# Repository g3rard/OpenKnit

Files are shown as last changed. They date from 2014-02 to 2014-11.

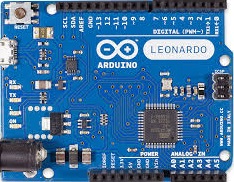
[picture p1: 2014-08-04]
Wally120/3Dmodel/OBJ_format/Wally120/Auduino_Leonardo_01.jpg

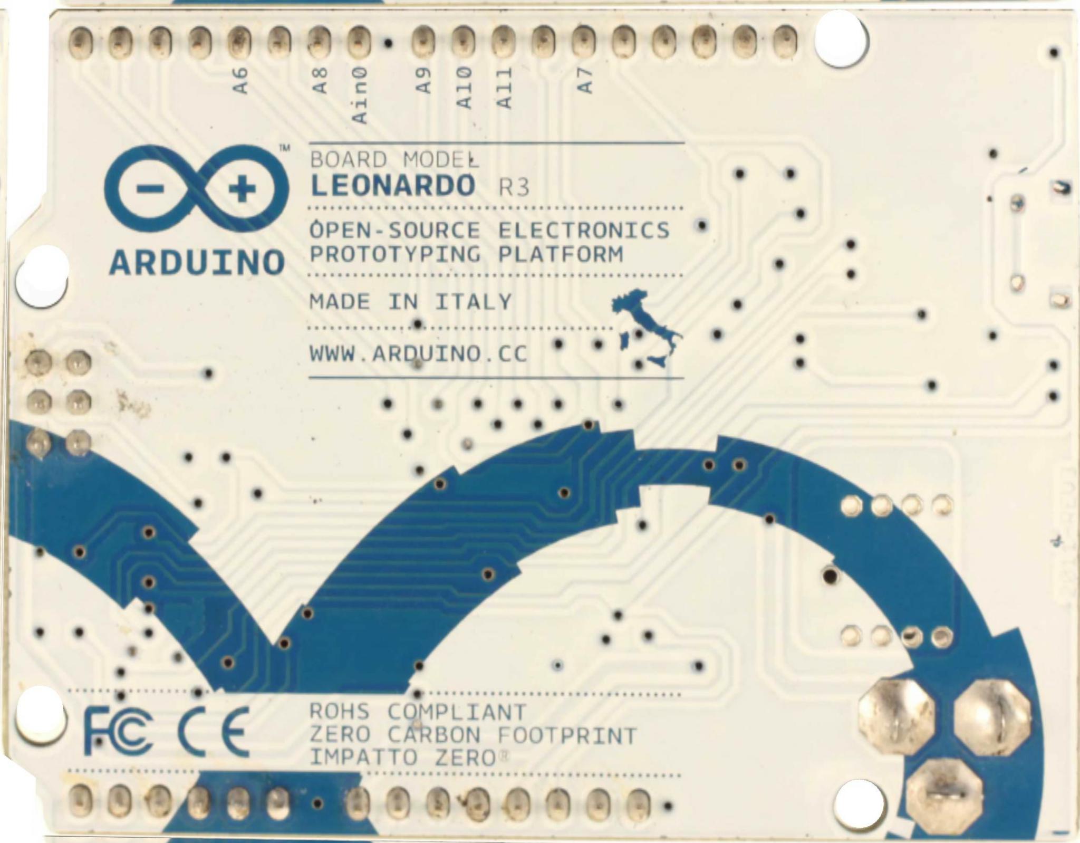
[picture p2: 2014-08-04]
Wally120/3Dmodel/OBJ_format/Wally120/Arduino_rear_1.jpg

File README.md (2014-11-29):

OpenKnit is a project that offers a new digital fabrication tool, an open-source knitting machine that can create ready-to-wear clothes from digital files. 

The documentation for the Wally340 is outdated, currently working on the development of the Wally120 since itÕs cheaper, smaller, easier to assemble and it works better. Although, the improvements of the Wally120 can be scaled up if you want to create bigger garments.

WARNING: this project is at an early stage of development, every piece of hardware and software is in beta version, testing and testing, if you are an adventurer this is a place for you.

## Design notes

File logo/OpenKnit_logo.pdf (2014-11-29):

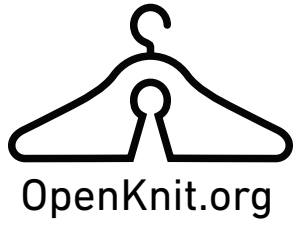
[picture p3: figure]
OpenKnit.org

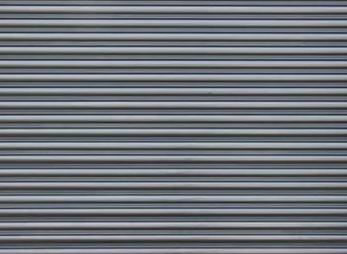
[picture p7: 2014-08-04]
Wally120/3Dmodel/OBJ_format/Wally120/M3.jpg

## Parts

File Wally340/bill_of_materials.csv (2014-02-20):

COMPONENT | UNITS | PRICE (€) | PROVIDER
 |  |  | LOCAL (Barcelona)
methacrylate | 1015x1525x3mm | 60 | http://plasticexpress.es/
lasercut | 1 | 100 | http://fablabbcn.org/
aluminum T profile 15x15 | 3582mm | 10.78 | http://www.hiperaluminio.com/
aluminum I profile 20x3 | 5505mm | 13.76 | http://www.hiperaluminio.com/
plastic parts | 500gr | 12.07 | http://www.reprapbcn.com/catalog/index.php/material-pla/pla-3mm.html
Arduino Leonardo | 1 | 21.78 | http://www.diotronic.com/raspberry-pi-arduino/arduino/placas/arduino-leonardo-w-headers_r_1080_26762.aspx
microinterrupter | 2 | 2.84 | http://www.diotronic.com/componentes-mecanicos/interruptores-conmutadores-pulsadores/microrruptores-final-de-carrera/microrrup-miniatura-3a125v-c-p_r_194_1820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
photo relfective sensor | 1 | 1.29 | http://www.ondaradio.es/producto/cny70-rohs-refleoptcouplgaas-ir-infrared-emitt-diodeplastcase-23579.aspx
hall effect sensor | 2 | 2.56 | http://www.ondaradio.es/producto/a1106euat-rohs-transistor-efecto-hall-sip-3-27327.aspx
bearing 608 | 1 | 2 | local hardware store or skateshop
threaded rod | 881mm | 1.5 | local hardware store
nuts and bolts | many | 20 | local hardware store
 |  |  | SPAIN
aluminum X profile 20x20 | 6870mm | 26.68 | http://www.motedis.es/shop/Perfil-ranurado/Perfil-20-Tipo-B-ranura-6/Perfil-20x20-Tipo-B-ran-6::999991.html
aluminum X profile 30x30 | 3000mm | 20.29 | http://www.motedis.es/shop/Perfil-ranurado/Perfil-30-Tipo-B-ranura-8/Perfil-30x30-Tipo-B-ran-8::99999432.html
aluminum X profile 40x40 | 3582mm | 34.76 | http://www.motedis.es/shop/Perfil-ranurado/Perfil-40-Tipo-I-ranura-8/Perfil-40x40L-Tipo-I-ran-8::999999.html
 |  |  | EUROPE (UK)
needles | 380 | 104.5 | http://www.bsk.co.uk/knitmastersilver-reed-sk120--sr120-xkn8-763-p.asp
 |  |  | CHINA (Aliexpress)
stepper driver A4988 | 1 | 5.28 | http://www.aliexpress.com/item/Stepstick-A4988-for-3D-printer-with-heat-sink-Reprap-Stepper-motor-driver-order-4-pcs-price/1053639333.html
stepper motor nema17 | 1 | 10.91 | http://www.aliexpress.com/item/4-Leads-Nema-17-Stepper-Motor-2800g-cm-12VDC-0-4A-CNC-Cutting-and-Mill-of/536727302.html
servomotor SG90 | 5 | 7.85 | http://www.aliexpress.com/item/Hot-sell-5X-SG90-9g-Mini-Micro-Servo-for-RC-for-RC-250-450-Helicopter-Airplane/1299439951.html
timing belt gt2 | 4m | 11.98 | http://www.aliexpress.com/item/Hot-sale-10meter-GT2-6mm-open-timing-belt-width-6mm-GT2-belt/1395064676.html
timing pulley gt2 | 1 | 7.3 | http://www.aliexpress.com/item/20GT2-6-timing-pulley-2pcs-20-teeth-6mm-width-5mm-bore-free-shipping/877902440.html
Vgroove bearing 623 | 24 | 46 | http://www.aliexpress.com/item/10pcs-3mm-V-Groove-Sealed-Ball-Bearings-0-118-inch-vgroove-bearing-623VV-3-12-4/947908627.html
 |  | 524.13 | € total

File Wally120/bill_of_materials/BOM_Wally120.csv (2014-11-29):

COMPONENT | UNITS | PRICE (€) | PROVIDER
 |  |  | LOCAL (Barcelona)
methacrylate | 810x635x3mm | 40 | http://plasticexpress.es/
lasercut | 1 | 40 | http://fablabbcn.org/
aluminum T profile 15x15 | 2*800mm | 10.78 | http://www.hiperaluminio.com/
aluminum I profile 25x3 | 3*800mm | 20.76 | Servei Estació
carbon fiber tensor | 120mm | 2 | Servei Estació
copper rod | 1.5x160mm | 1 | Servei Estació
plastic parts | 300gr | 8 | http://www.reprapbcn.com/catalog/index.php/material-pla/pla-3mm.html
Arduino Leonardo | 1 | 21.78 | http://www.diotronic.com/raspberry-pi-arduino/arduino/placas/arduino-leonardo-w-headers_r_1080_26762.aspx
microinterrupter | 2 | 1.72 | http://www.diotronic.com/componentes-mecanicos/interruptores-conmutadores-pulsadores/microrruptores-final-de-carrera/microrrup-miniatura-3a125v-c-p_r_194_1820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
rotary encoder | 1 | 1.6 | http://www.ondaradio.es/producto/ec12e12204-rohs-alps-encoder-vertical-12-det-12ppr-21700.aspx
stepper driver A4988 | 1 | 9 | http://www.reprapbcn.com/en/catalog/product/white-pololu-stepper-motor-driver-carrier-heatsink
stepper motor nema17 | 1 | 13 | http://www.reprapbcn.com/es/catalog/product/nema-17-stepper-not-crimped
timing pulley gt2 | 1 | 4.2 | http://www.reprapbcn.com/es/catalog/product/t25-10mm-aluminium-pulley
threaded rod | 16+16+17+17+22+22=110cm | 1.5 | local hardware store
bearing 608 | 1 | 2 | local hardware store
nuts and bolts | many (list soon) | 10 | local hardware store
paper clips | 60 | 1 | local hardware store
wire rod | 2x50mm | 1 | local hardware store
 |  |  | SPAIN
aluminum X profile 20x20 | 800mm*4=3200 | 14 | http://www.motedis.es/shop/Perfil-ranurado/Perfil-20-Tipo-B-ranura-6/Perfil-20x20-Tipo-B-ran-6::999991.html
aluminum X profile 30x30 | (162*2 (one side threaded))+(310*2)+(800*2) = 2534 | 21 | http://www.motedis.es/shop/Perfil-ranurado/Perfil-30-Tipo-B-ranura-8/Perfil-30x30-Tipo-B-ran-8::99999432.html
 |  |  | EUROPE
needles | 120 | 50 | http://www.bsk.co.uk/knitmastersilver-reed-sk120--sr120-xkn8-763-p.asp
small servo | 6 | 30 | http://hobbyking.com/hobbyking/store/__42775__HK_15178B_Digital_MG_Servo_13_5g_1_5kg_0_08s_EU_Warehouse_.html
 |  |  | CHINA (Aliexpress)
timing belt gt2 | 192cm | 2.27 | http://www.aliexpress.com/item/Hot-sale-10meter-GT2-6mm-open-timing-belt-width-6mm-GT2-belt/1525204050.html
Vgroove bearing 623 | 16 | 32 | http://www.aliexpress.com/item/10pcs-3mm-V-Groove-Sealed-Ball-Bearings-0-118-inch-vgroove-bearing-623VV-3-12-4/947908627.html
 |  | 338.61 | € total

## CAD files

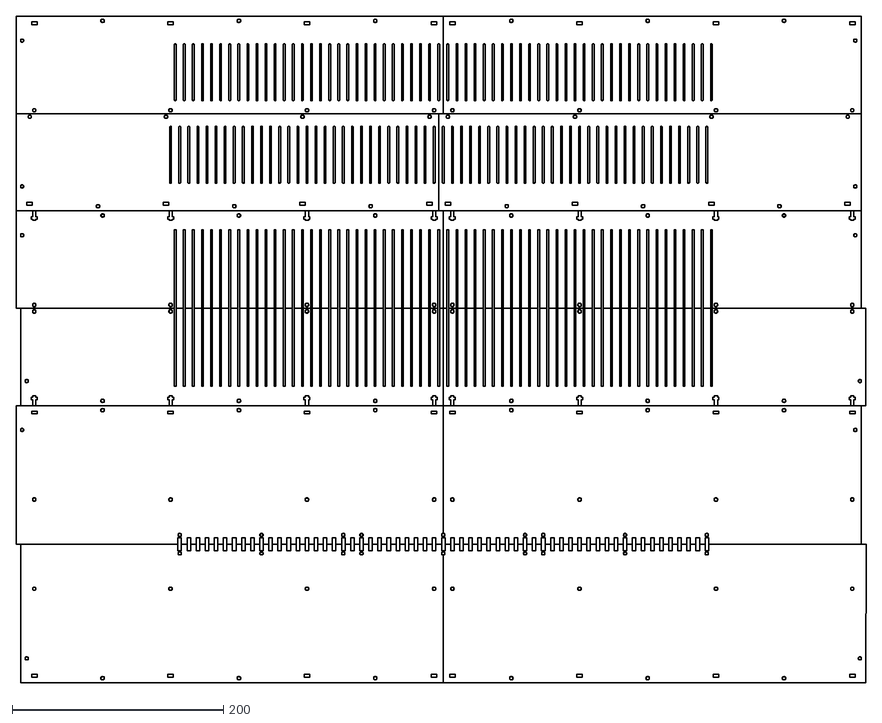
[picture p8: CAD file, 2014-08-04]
Wally120/lasercut/lasercut_Wally120.dxf
804.3 x 630.8

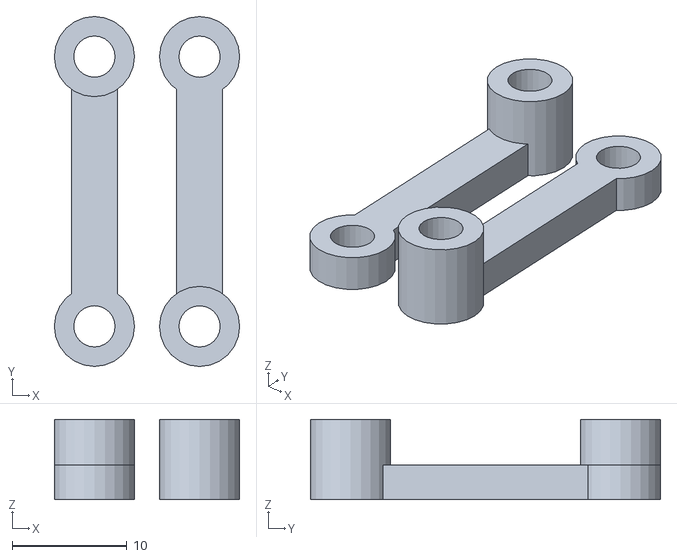
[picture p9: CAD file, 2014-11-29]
Wally120/STLs/sled_arms(2).stl
16.2 x 30.6 x 7.00

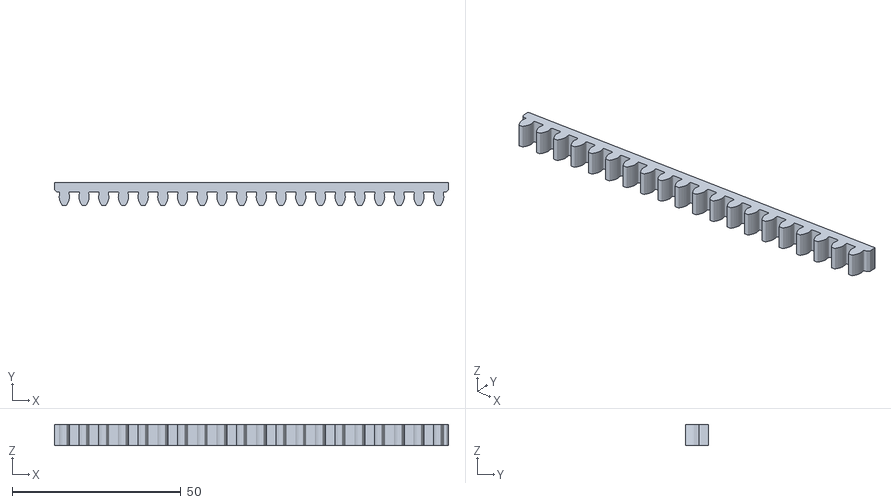
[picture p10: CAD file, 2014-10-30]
Wally120/STLs/encoder_rack(6).stl
116.8 x 6.89 x 6.30

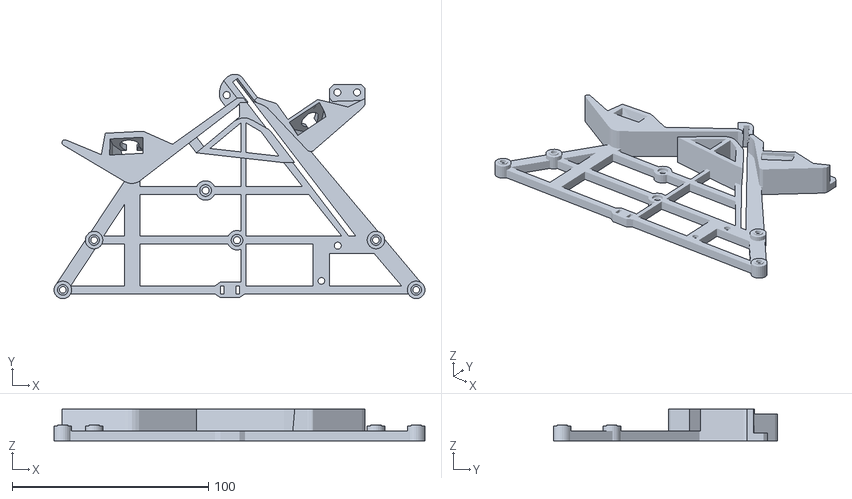
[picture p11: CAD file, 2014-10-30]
Wally120/STLs/carriage(2).stl
189.1 x 114.4 x 16.2

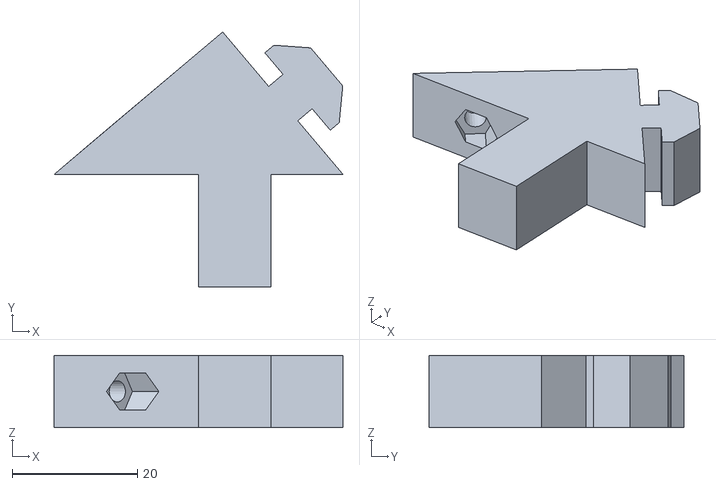
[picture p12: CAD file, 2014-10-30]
Wally120/STLs/leg(4).stl
46.2 x 40.8 x 11.5

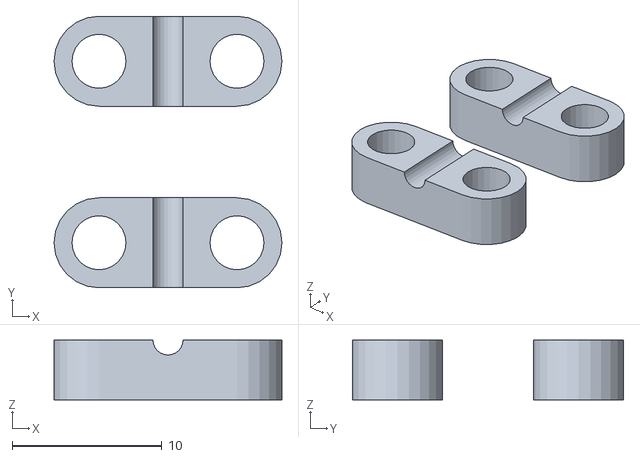
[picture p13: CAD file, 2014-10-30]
Wally120/STLs/tensor_head(1).stl
15.2 x 18.1 x 4.00

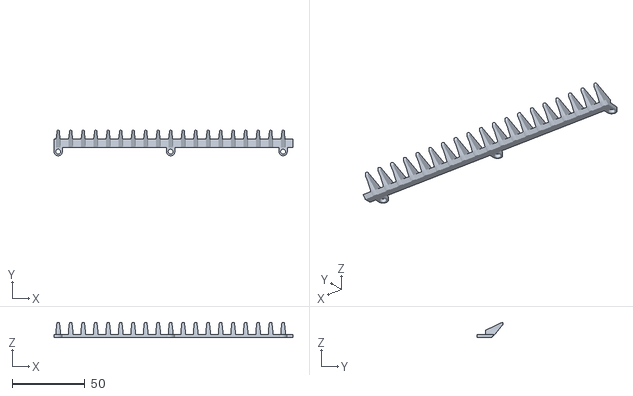
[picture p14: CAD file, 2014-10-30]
Wally120/STLs/teeth_left_side(2).stl
164.5 x 17.7 x 10.5

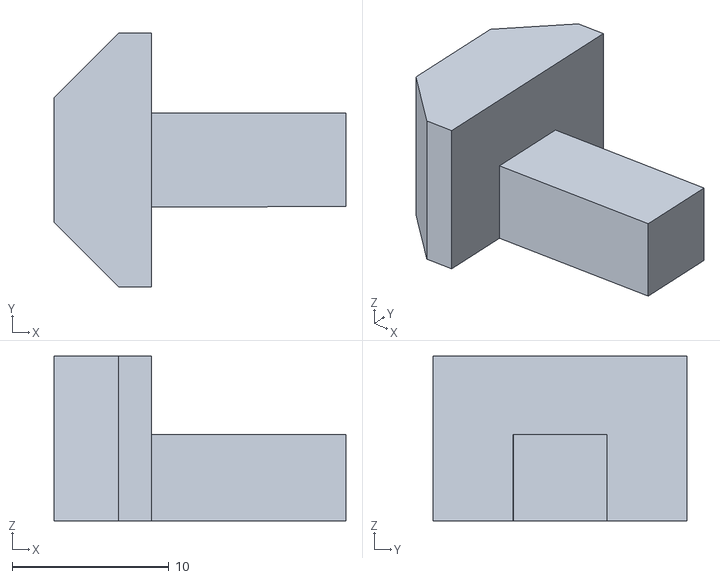
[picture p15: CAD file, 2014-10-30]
Wally120/STLs/L_2020-3030(4).stl
18.6 x 16.2 x 10.5

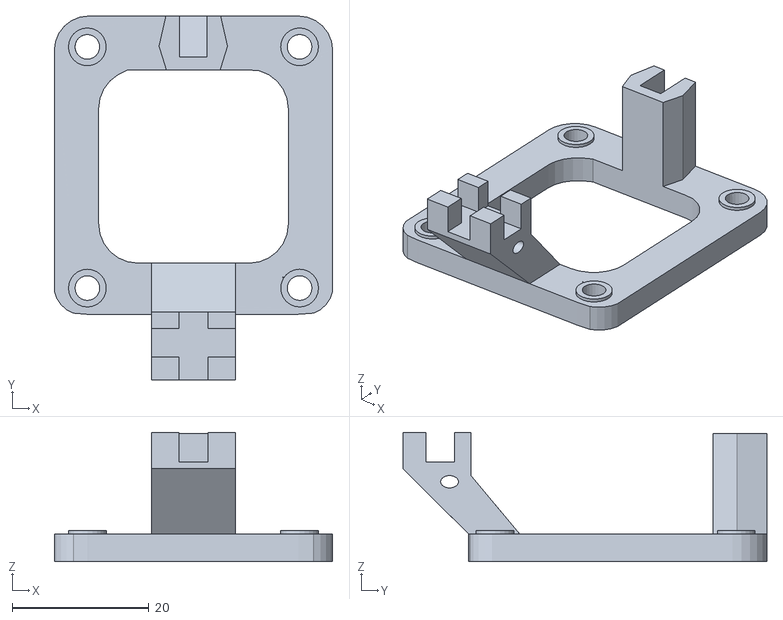
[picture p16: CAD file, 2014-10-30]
Wally120/STLs/yarn_carrier(1).stl
40.7 x 53.2 x 18.9

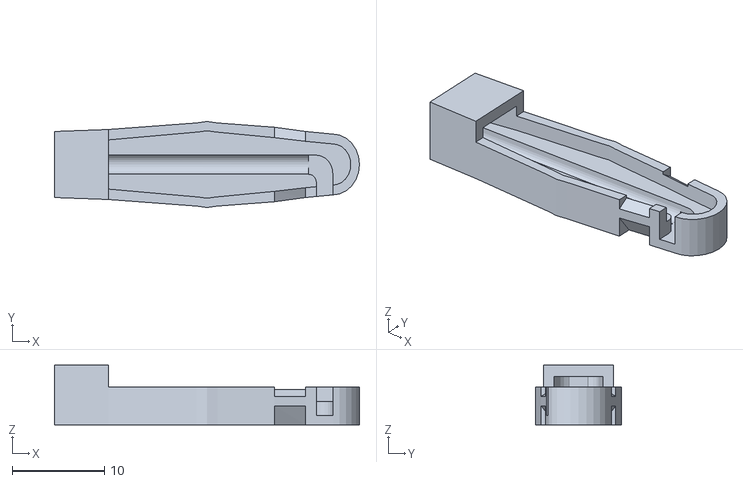
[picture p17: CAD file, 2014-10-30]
Wally120/STLs/servo_beam_mount(2).stl
33.0 x 9.32 x 6.45

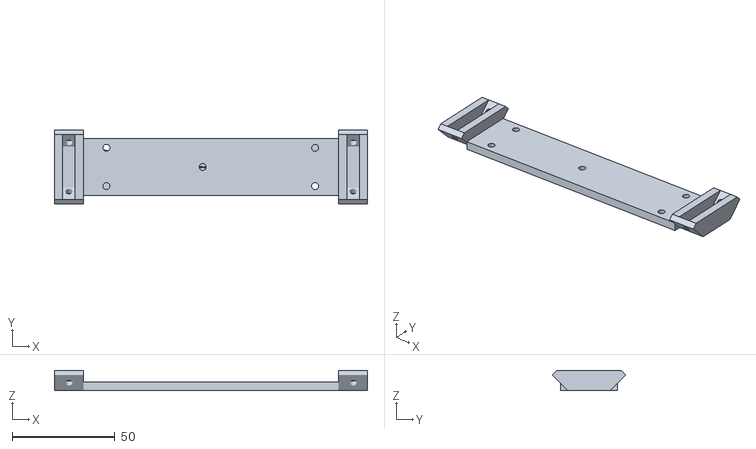
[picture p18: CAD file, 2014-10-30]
Wally120/STLs/top_plate_bearings(1).stl
152.0 x 35.7 x 9.74

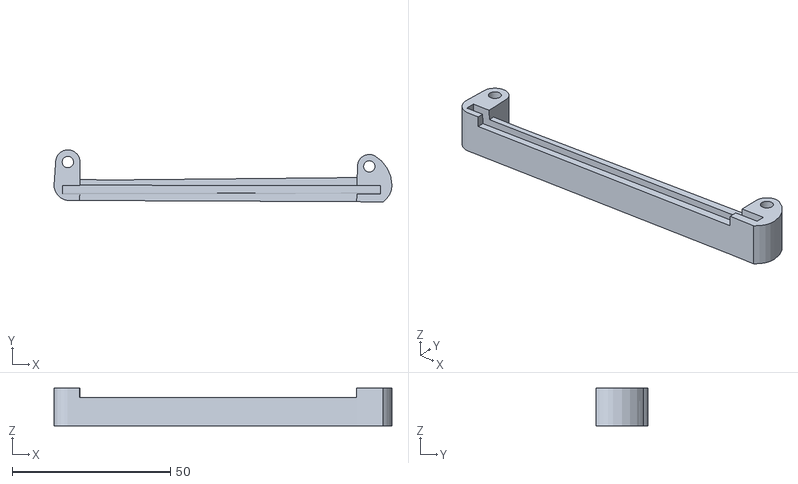
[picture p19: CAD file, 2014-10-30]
Wally120/STLs/slider_guide(2).stl
106.9 x 16.6 x 12.0

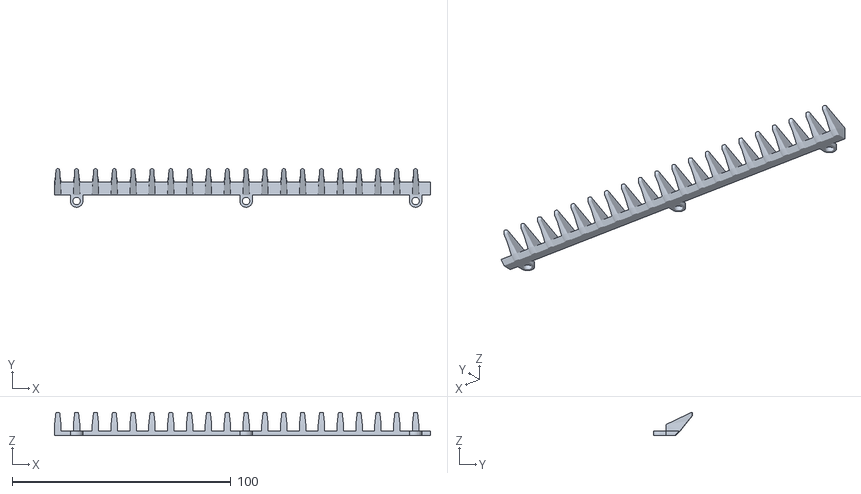
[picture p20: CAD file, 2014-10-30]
Wally120/STLs/teeth(4).stl
171.7 x 17.7 x 10.5

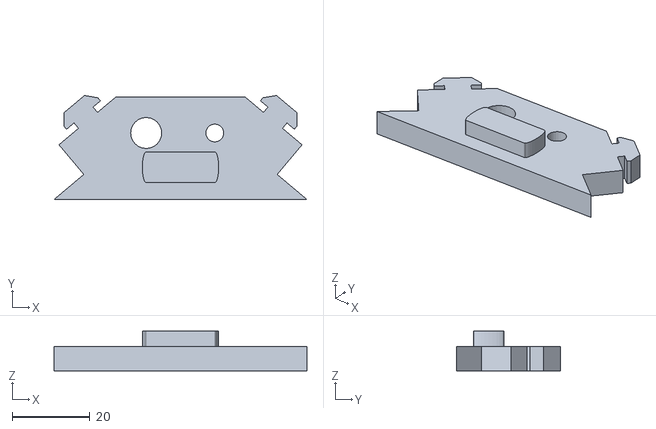
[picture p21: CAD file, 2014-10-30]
Wally120/STLs/space_invaders(2).stl
65.3 x 26.8 x 10.2

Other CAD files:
Wally120/STLs/cable_grommet(1).stl
Wally120/STLs/tensor_table_bottom(1).stl
Wally120/STLs/tensor_table_Top(1).stl
Wally120/STLs/tensor_table_wax(1).stl
Wally120/STLs/2020nut(37).stl
Wally120/STLs/3030nut(7).stl
Wally120/STLs/Arduino_mount(1).stl
Wally120/STLs/N_mount(2).stl
Wally120/STLs/bearing608_mount(1).stl
Wally120/STLs/belt_clamp(1).stl
Wally120/STLs/carriage_servo_mount(2).stl
Wally120/STLs/encoder_pinion(1).stl
Wally120/STLs/sled(2).stl
Wally120/STLs/sled_mount(2).stl
Wally120/STLs/slider(2).stl
Wally120/STLs/stepper_mount(1).stl
Wally120/STLs/stepper_mount_back(1).stl
Wally120/STLs/top_plate(1).stl
Wally120/STLs/top_plate_servo_mount(1).stl
Wally120/STLs/wax_holder(1).stl

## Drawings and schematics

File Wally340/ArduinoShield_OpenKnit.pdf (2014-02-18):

## Arduino Leonardo shield for an OpenKnit machine

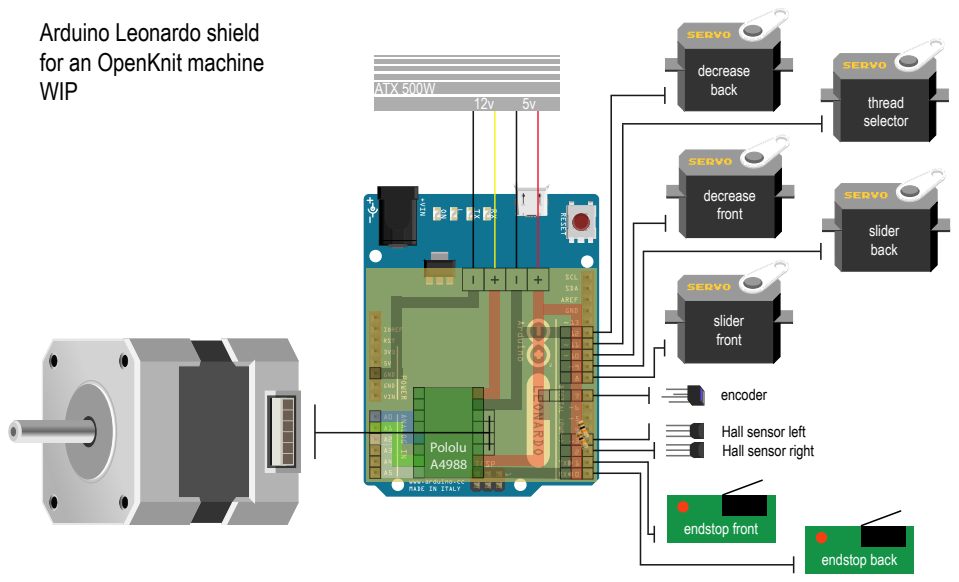
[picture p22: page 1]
slider front; thread selector; decrease front; decrease back; WIP; slider back; endstop front; endstop back; Pololu A4988; ATX 500W

encoder
Hall sensor left
Hall sensor right

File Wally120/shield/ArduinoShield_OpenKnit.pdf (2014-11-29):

## Arduino Leonardo shield for an OpenKnit machine

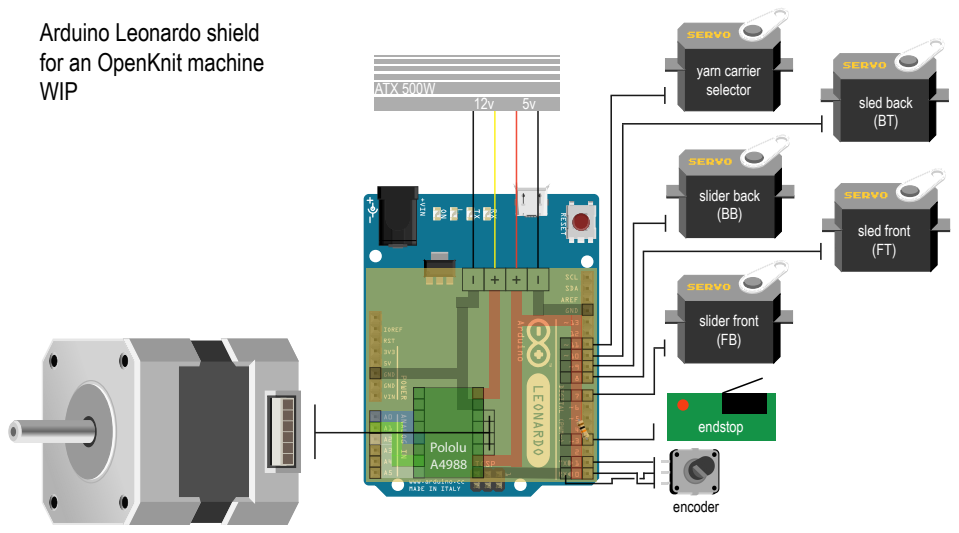
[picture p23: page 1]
slider front; sled back (BT); slider back (BB); yarn carrier selector; WIP; encoder; sled front (FT); slider front (FB); endstop; Pololu A4988; ATX 500W

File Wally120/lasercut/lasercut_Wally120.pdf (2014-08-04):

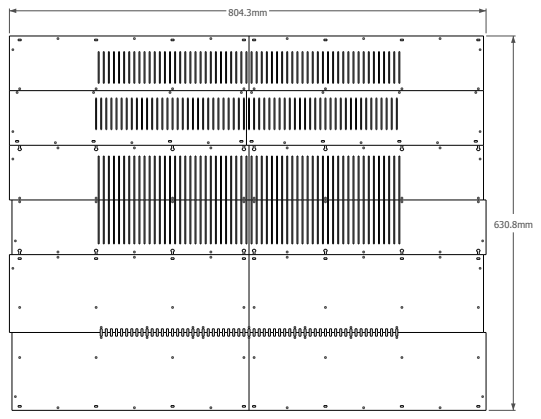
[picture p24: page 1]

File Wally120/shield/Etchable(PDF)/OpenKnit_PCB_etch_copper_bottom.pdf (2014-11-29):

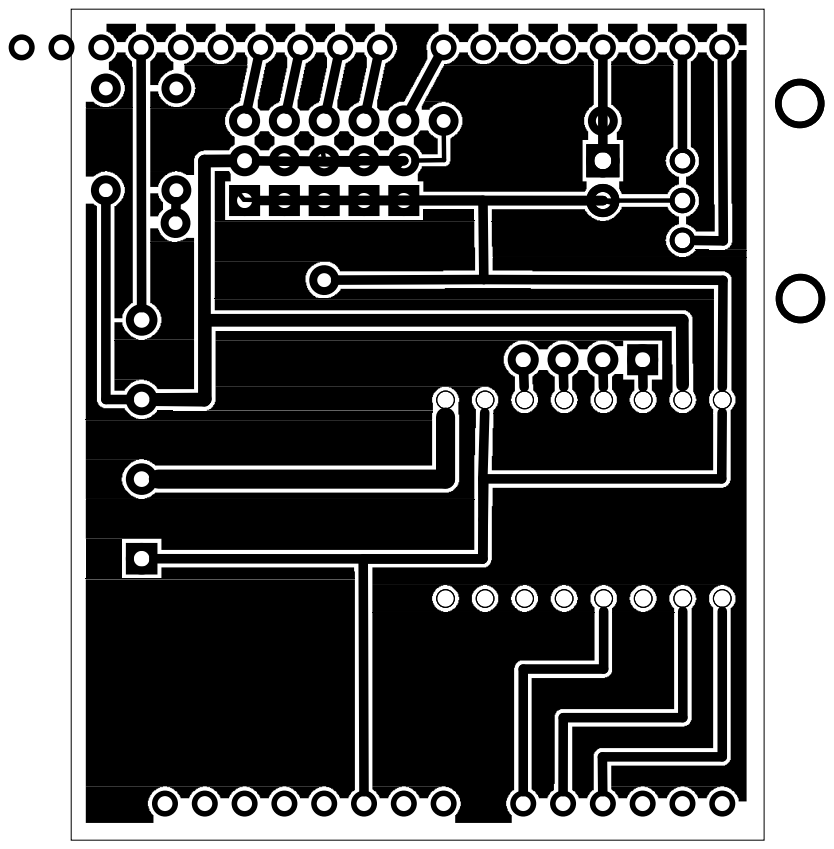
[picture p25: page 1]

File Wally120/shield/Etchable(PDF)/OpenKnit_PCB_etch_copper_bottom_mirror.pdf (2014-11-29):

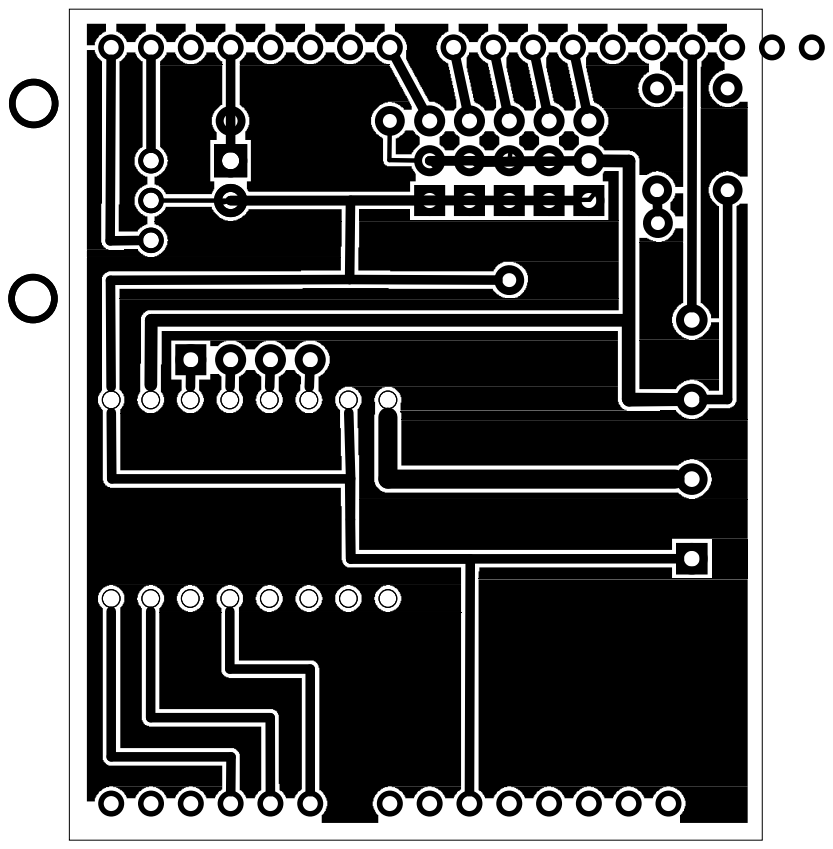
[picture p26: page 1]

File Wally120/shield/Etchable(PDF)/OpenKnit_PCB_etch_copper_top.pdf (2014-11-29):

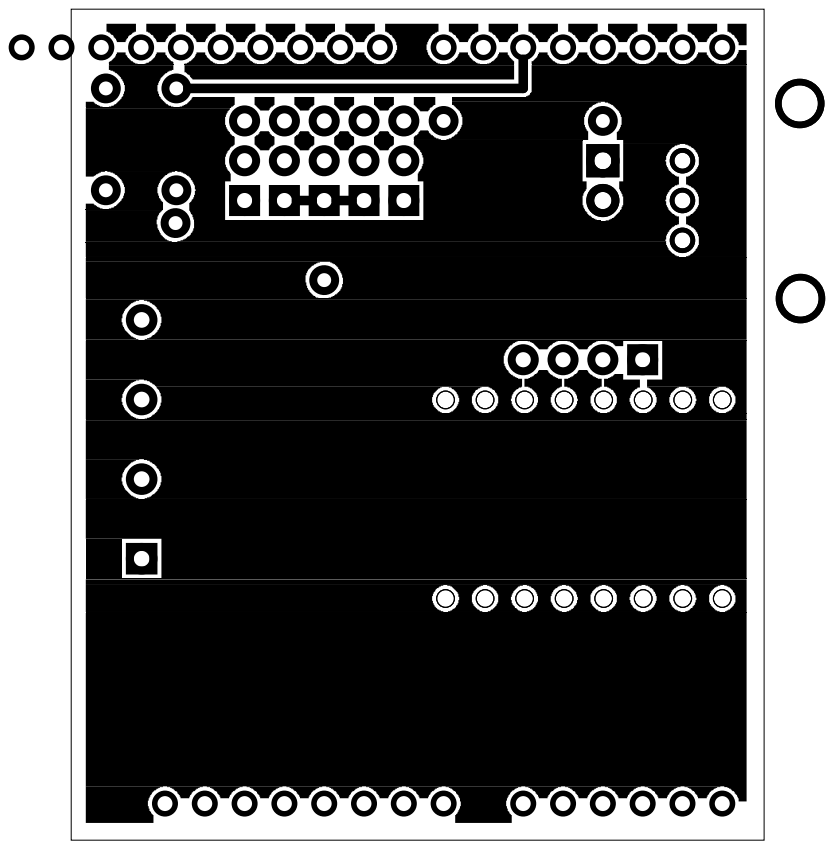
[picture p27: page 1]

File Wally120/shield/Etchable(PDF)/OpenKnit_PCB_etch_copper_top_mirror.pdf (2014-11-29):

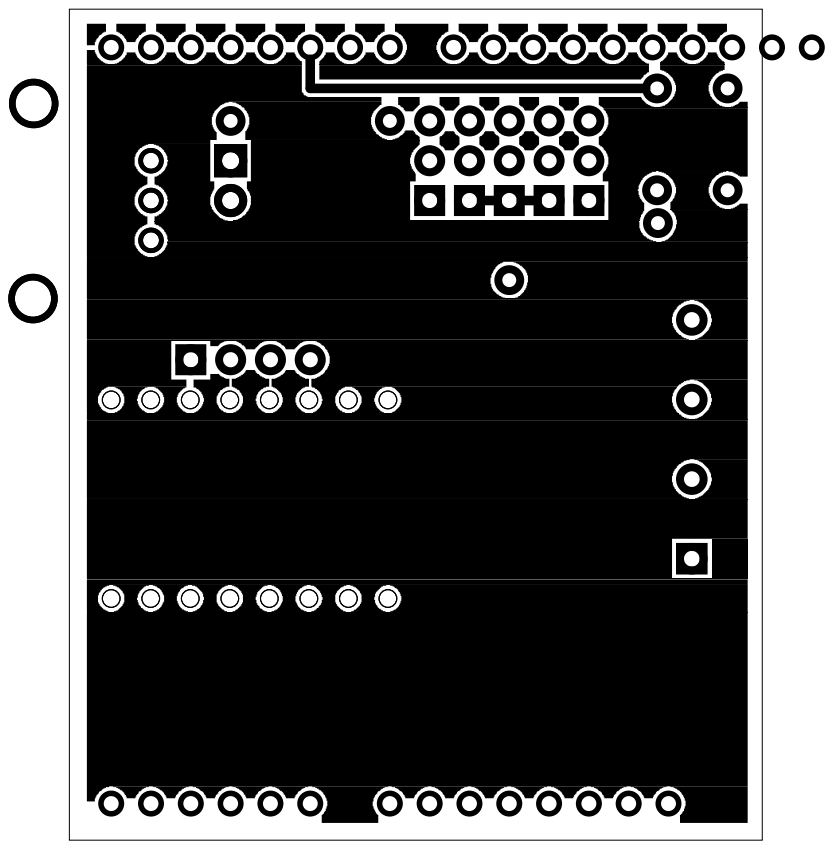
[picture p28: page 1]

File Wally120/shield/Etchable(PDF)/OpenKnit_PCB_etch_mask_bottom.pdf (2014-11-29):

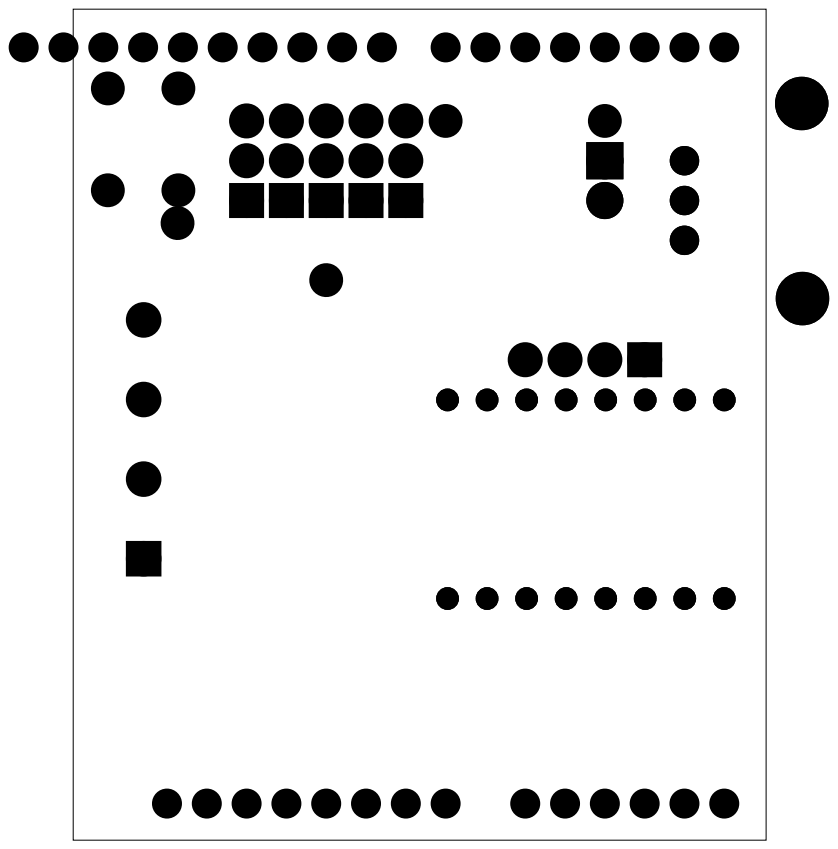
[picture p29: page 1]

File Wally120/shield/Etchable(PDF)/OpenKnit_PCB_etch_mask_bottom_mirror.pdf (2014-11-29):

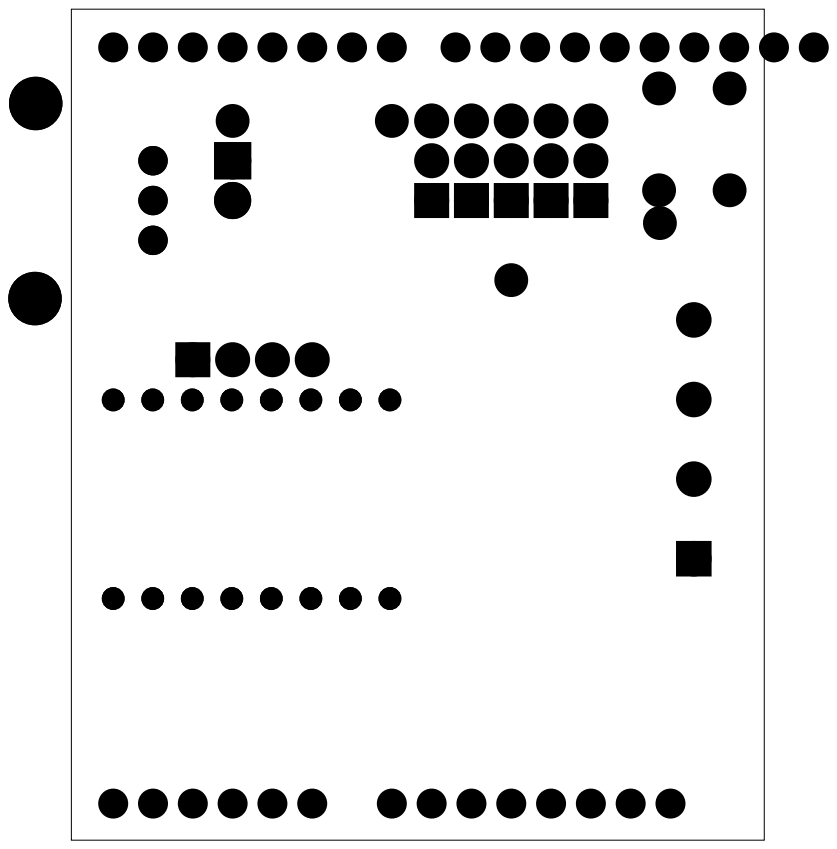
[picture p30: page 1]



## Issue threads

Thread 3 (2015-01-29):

Purpose of the encoder and changes to the code

DomAmato, 2015-01-29:
Sorry if I am naive but is the encoder necessary? I would understand if you were using a DC motor that had no positional awareness but if you use a stepper library like PJRC's accelStepper you can keep track of the position of the steppers or even just use a step variable and then just use the normal Stepper library from Arduino. It seems like one less thing to worry about hardware wise and in the code.

The code as it is is sort of a mess, is there any plans to implement a protocol to control things from a computer input or SD card. Like a common control language such as g-code or using a preexisting protocol like firmata. as of now it just runs a preset clothing item which is fine but it seems like it would benefit from a set firmware and then have software clients that can tell it the type of items to knit.

LokiMetaSmith, 2015-02-04:
It depends on how fast the machine is going. Steppers can lose a step for mechanical reasons, like going too fast or getting in a high friction spot. With an encoder, the software can make minor corrections or halt before that happens, which allows the machine to reliably rotate the motors faster.

I'm keeping an eye on this project, but I've not built one yet. I would use g-code so you can easily incorporate some of the excellent reprap projects into this one. It would require re-writing a slicer but that needs to happen regardless.

DomAmato, 2015-02-04:
I'm not sure gcode would be the best method. Its 1 axis movement and you would have to map values to handle the servos that aren't particularly standardized. I think in terms of CN machines this one has some unique features that 3d printers or cnc's don't have and so a less robust and succinct protocol would better serve it. I mentioned it but now that I think about it i don't think gcode would be right for the reasons I stated above.

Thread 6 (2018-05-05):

needle

zzllabcd, 2018-05-05:
the size of the needle in the bill list is no longer to sell, which size of needle can be instead of ?

futureblot, 2020-01-02:
I'm curious if anyone knows the specifications of the needles that were in the bill and if we can maybe find them elsewhere or even 3D print them???

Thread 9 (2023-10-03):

Is this project dead?

Josef-Reichardt, 2023-10-03:
I'm very interested building a knitting machine by my own and searching for some open source projects which I can use as a starting point or to find a community.

As far as I've read this open source project was transformed into a company (knitterate.com) which sells knitting machines for ~ $15k. Ist this correct? That's no option for me just want to do this as a hobby.

Can someone lead me to active projects for (open source) knitting machines? Im spacially interested in knitting motif socks.

hamsterwoede, 2023-10-03:
As far as I know it’s dead. To my knowledge there aren’t any open source flatbed knitting machines. Although I don’t have any personal experience with them, there has been a resurgence of 3D printed sock knitted machines. Look for “sock knitting machine 3d print” and you’ll find a few. Don’t think they’ll do patterning though, bu I could be wrong. Personally I prefer to work on a “regular” double bed machine. Passap DM80’s and Brother kh-890’s usually can be found quite cheap second hand.

If you’re not familiar with machine knitting, be prepared to put some time in. It’s not as easy as it seems ;-)

LokiMetaSmith, 2023-10-03:
Here's the Open Source Ecology page that lists further resources.
https://wiki.opensourceecology.org/wiki/Knitting_Machine

There's a bunch of community driven open source projects moving to closed source as they progress that's pretty depressing. However, a project like this only dies when interest in it ends, so feel free to fork it and make it your own!

wasteoinc, 2023-10-04:
I got a brother 930 second hand but never had the time to fully get into it,

Openknit works so even though the project further dev is dead, it's still usable I would say.

But yes be prepared to put some time, if you have never knitted like me :)

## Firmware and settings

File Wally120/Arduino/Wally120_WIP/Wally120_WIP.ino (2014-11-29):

//stepper
#define speedRotation 1000  //speed of the motor rotation
int steps = A1;
int dir = A2; 
int reset = A0;
int stepsRotation = 30000; //steps that the stepper does 
int i;
int j;
int h;
boolean dirRotation = LOW;  //direction of rotation

//encoder
int encoderPin1 = 0;
int encoderPin2 = 1;
volatile int lastEncoded = 0;
volatile long encoderValue = 0;
long lastencoderValue = 0;
int lastMSB = 0;
int lastLSB = 0;
int increment = 1;

int numberRows = 0;
int needleBed = 1;           //front needle bed = 1 , back needle bed = 2
//(to create tubular sections)the knitting carriage have two identical systems, 
//one operating in the front needle bed and the other in the back, they never operate at the same time.
//carriage on the front needle bed operates only going to the left, while going to the right
//the front systems is "deactivated" and the carriage only operates in the back needle bed

//servo
#include <Servo.h> 
Servo servoFB; 
Servo servoFT;
Servo servoBB;
Servo servoBT;
Servo servoSelection; //not used with Wally120 since it has only one Yarn Carrier

int servoFB_in = 67;  
int servoFB_out = 99; 
int servoFT_in = 80; 
int servoFT_out = 155; 

int servoBB_in = 82;
int servoBB_out = 112;
int servoBT_in = 80;
int servoBT_out = 120;


void setup() {
  Serial.begin (9600);

  //stepper
  pinMode(steps, OUTPUT); 
  pinMode(dir, OUTPUT); 
  pinMode(reset, OUTPUT);

  //encoder
  pinMode(encoderPin1, INPUT); 
  pinMode(encoderPin2, INPUT);
  digitalWrite(encoderPin1, HIGH); 
  digitalWrite(encoderPin2, HIGH); 
  attachInterrupt(2, updateEncoder, CHANGE); 
  attachInterrupt(3, updateEncoder, CHANGE);

  //end stop
  attachInterrupt(0, endStop, CHANGE);  //pin 3

  //servo
  servoFB.attach(7);   // servo in the front needle bed selecting needles
  servoFT.attach(8);   // servo in the front needle bed stopping the loops rising up
  servoBB.attach(9);   // servo in the back needle bed selecting needles
  servoBT.attach(10);   // servo in the back needle bed stopping the loops rising up

  homing();  //carriage goes home before anything else to get coordinatee zero
}

void loop(){ 
  oneTube();  //scarfs, beanies, dresses (no sleeves), socks, etc
}

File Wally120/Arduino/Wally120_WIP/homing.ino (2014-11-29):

// brings carriage to the rightmost, needle 0

void homing() {

  //servos
  servoFB.write(servoFB_out);
  delay (20);
  servoFT.write(servoFT_out);
  delay (20);
  servoBB.write(servoBB_out); 
  delay (20);
  servoBT.write(servoBT_out);
  delay (20);

  //CW right
  digitalWrite(reset, LOW);    
  delay(10);
  digitalWrite(reset, HIGH);   
  digitalWrite(dir, HIGH);

  for ( j = 0; j<stepsRotation; j++)       
  {
    digitalWrite(steps, HIGH);  
    digitalWrite(steps, LOW);   
    delayMicroseconds(speedRotation); 
  } 

  needleBed = 1;   //carriage is on the right so the machine can only knit going to the left, 
  //so it knits on the front needle bed.
} 

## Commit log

2014-02-01 deleta arduino
2014-02-01 readme arduino
2014-02-01 Arduino code
2014-02-18 electronics diagram for creating a shield for Arduino Leonardo
2014-02-18 circuit diagram for creating a shield for Arduino Leonardo
2014-02-18 step by step manual to assemble the machine
2014-02-20 list of every component with provider and price
    [bill_of_materials.csv]
2014-08-04 Wally120 is a new OpenKnit machine
    [2020nut(37).stl, 3030nut(11).stl, Arduino_mount.stl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]
2014-11-29 Wally120 is at an early development stage
    [BOM_Wally120.csv, OpenKnit_PCB.fzz, sled_arms(2).stl]
